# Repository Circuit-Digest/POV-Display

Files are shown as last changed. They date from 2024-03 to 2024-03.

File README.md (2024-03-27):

# [POV Display](https://circuitdigest.com/microcontroller-projects/diy-pov-display-using-ESP32-Arduino)
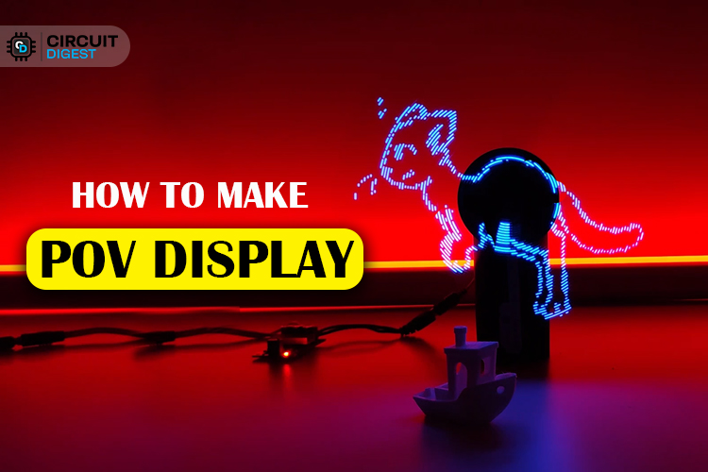
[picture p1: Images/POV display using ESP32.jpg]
image_tooltip

<br>

<br>

<be>

[DIY POV Display Tutorial using ESP32 Arduino](https://circuitdigest.com/microcontroller-projects/diy-pov-display-using-ESP32-Arduino)

[POV Display full Yoututbe Video](https://www.youtube.com/embed/gkemkTWuw_Q)

[<h1>Click here](https://circuitdigest.com/tags/ESP32) For other ESP32 tutorials.</h1>

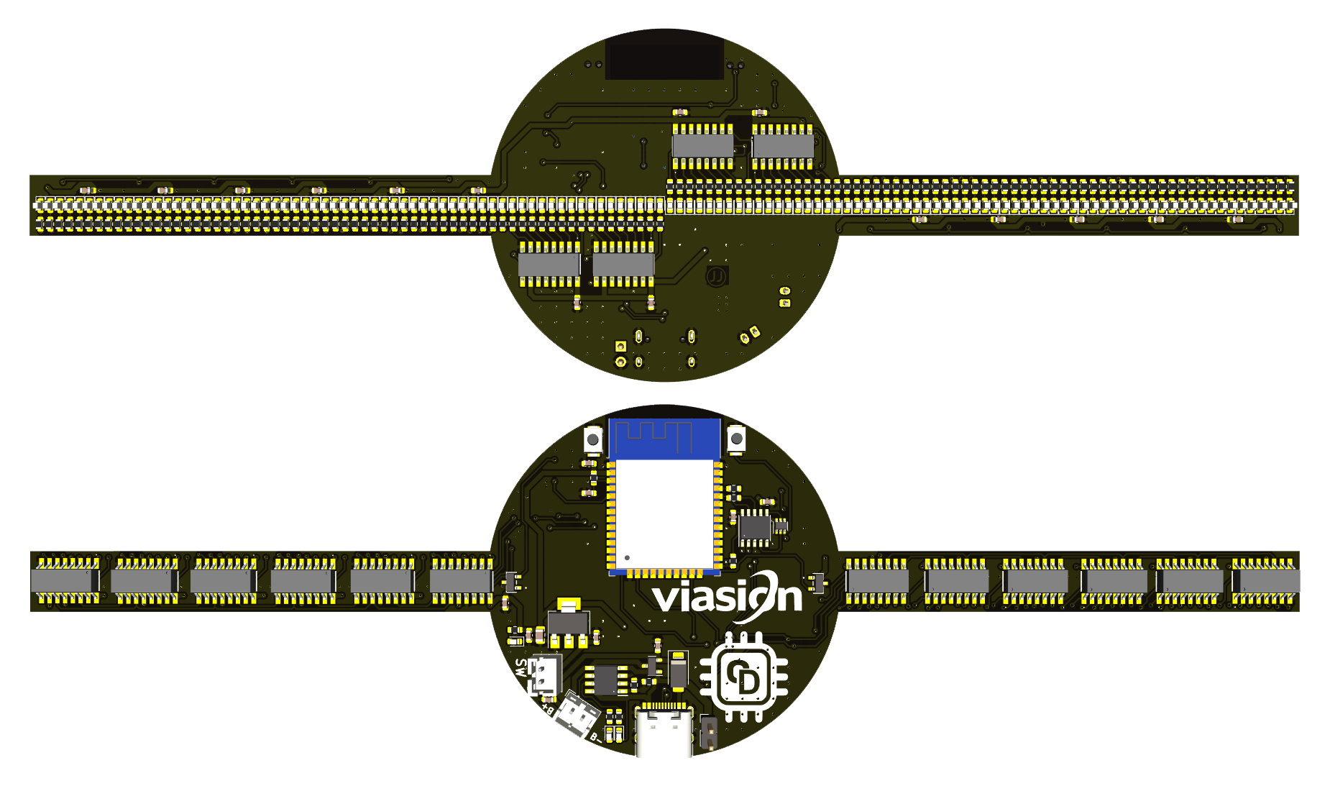
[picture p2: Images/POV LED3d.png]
image_tooltip

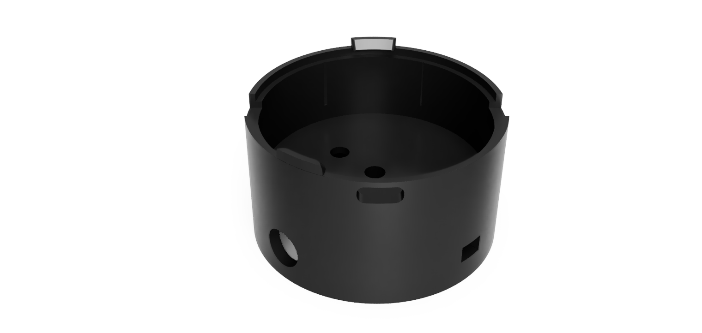
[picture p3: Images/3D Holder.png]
image_tooltip
<br>
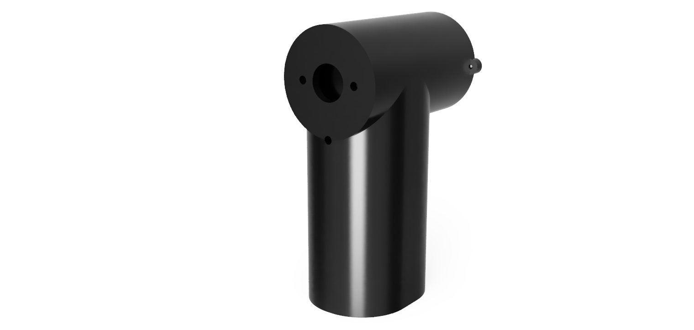
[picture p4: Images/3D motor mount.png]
image_tooltip
<br>
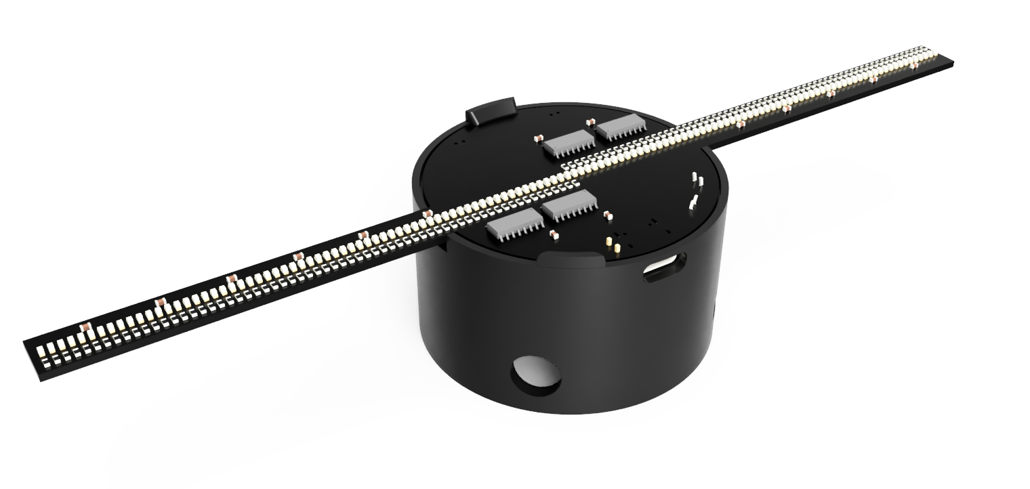
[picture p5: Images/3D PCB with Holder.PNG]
image_tooltip
<br>
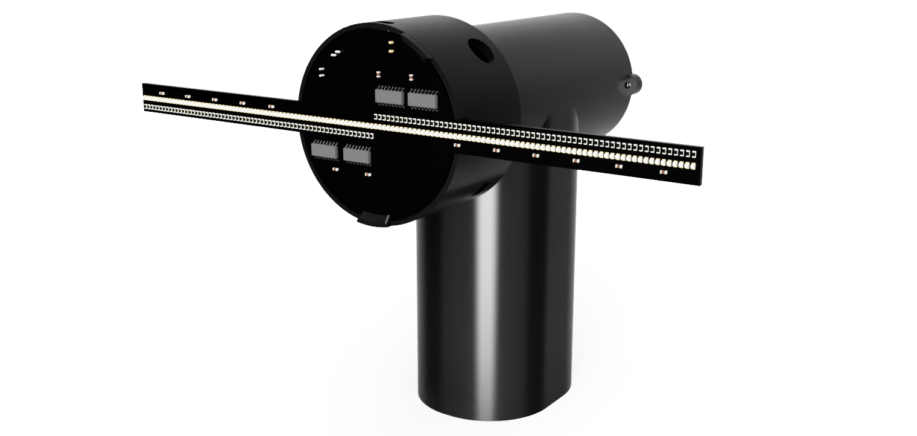
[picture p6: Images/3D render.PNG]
image_tooltip
<br>
<br>
<br>
<br>
Persistence of Vision is a fundamental principle that allows our eyes to perceive continuous motion from separate images, a concept crucial to the illusion of motion in cinema. When I was a kid, I was always fascinated with it. So, in this project, we are going to use this fascinating optical phenomenon to create a cool-looking POV Display. You must have seen a lot of such projects on the web, but most of them are limited to very low resolution and just display some texts and geometries. We plan to create a POV display that is not limited to just texts or simple shapes. Ours will be able to display images and animations with a resolution of 128 pixels. We have settled with this resolution because it's the sweet spot where we can get decent image quality and it would be easier to build.
 We settled on the ESP32 module as the brain of this display, because it is cheap, easy to get and powerful enough to run the display. The display will have two rotating arms, each outfitted with 64 LEDs, to create a total resolution of 128 pixels. The display will rotate at a constant speed, with the LEDs flashing in meticulously orchestrated patterns, controlled by the ESP32 microcontroller. This synchronization allows the display to generate images or text that appear to hover in mid-air, producing a smooth, continuous visual experience. 

<br>
[Note: As this projects are very simple we are only providing the code, schemaitic, and a few essential images if you want to get the images or code explanations do check out the Circuit Digest website.
<br>
<br>

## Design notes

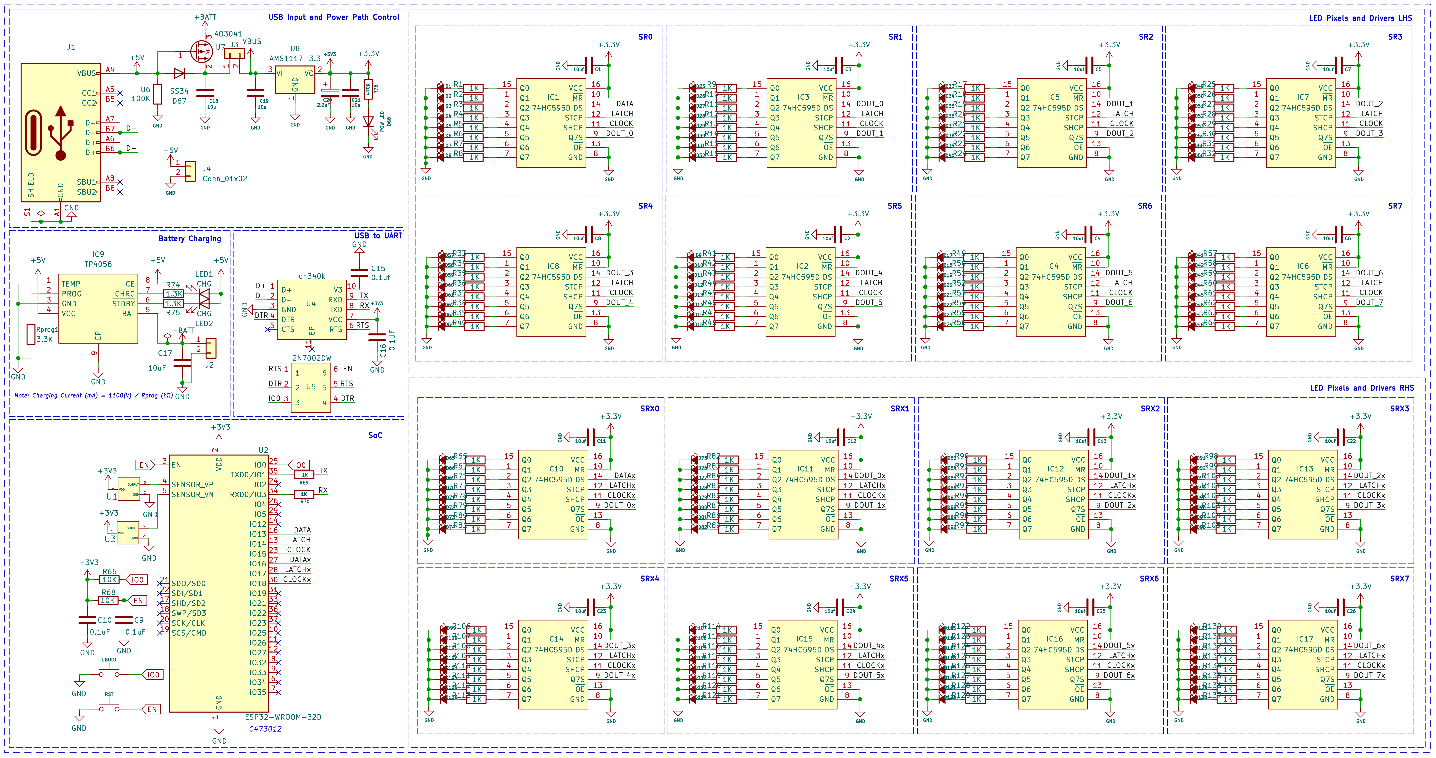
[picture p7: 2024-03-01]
PCB/Docs/Schematics POV Display.png

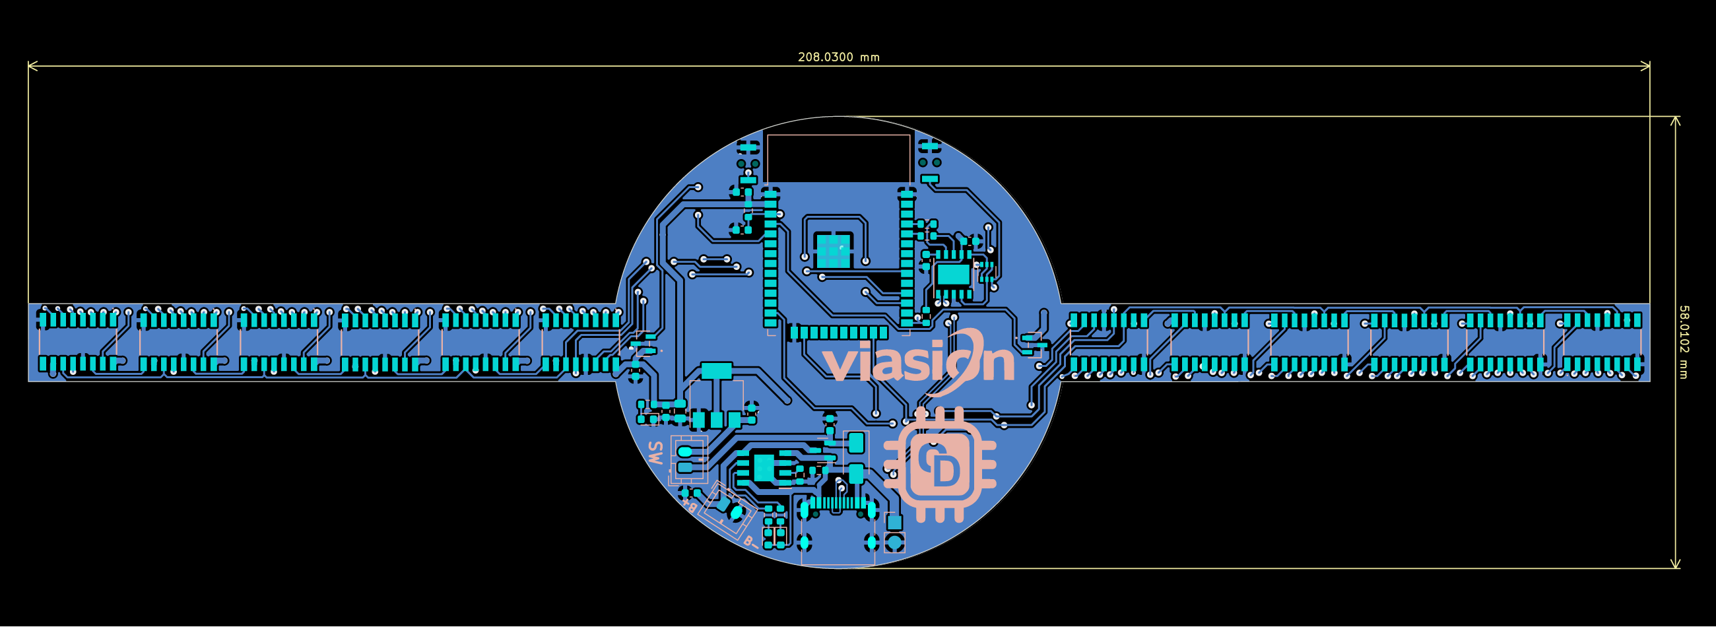
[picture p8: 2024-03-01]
PCB/Docs/POV LED-B_Cu.png

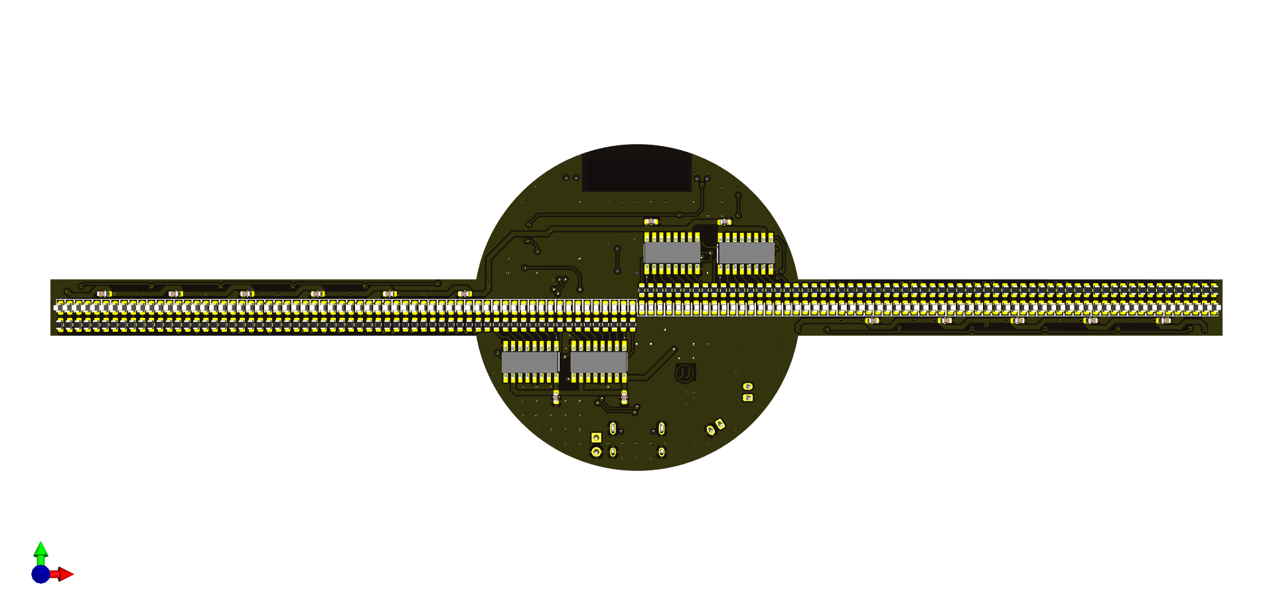
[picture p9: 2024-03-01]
Images/POV LED3d top.png

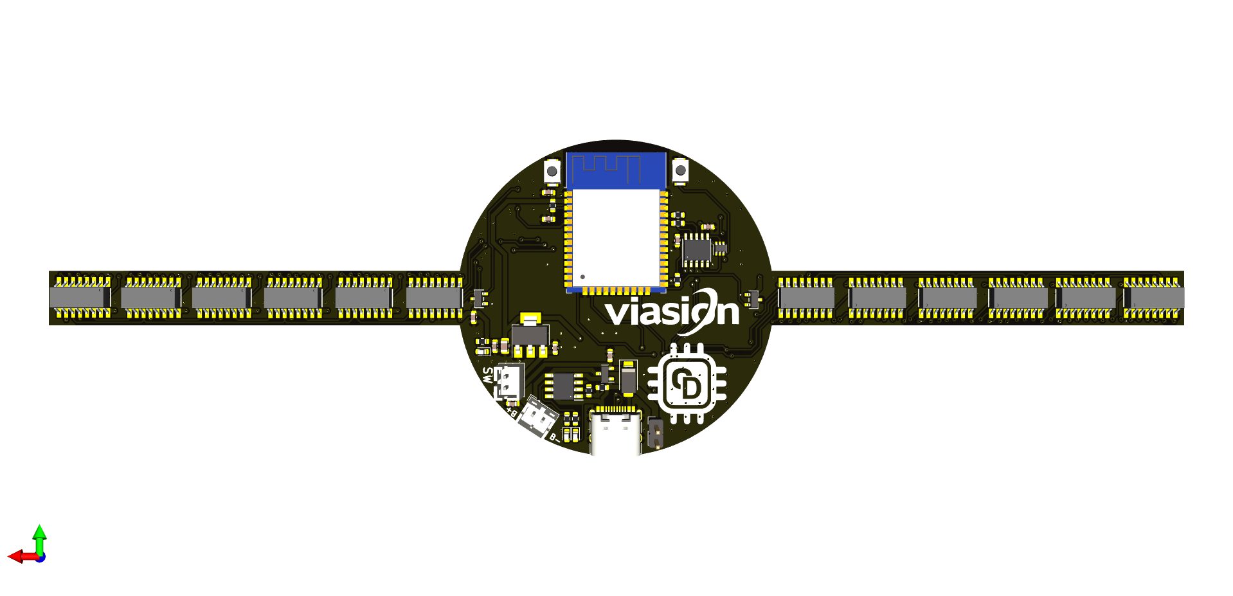
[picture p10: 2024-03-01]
Images/POV LED3d bottom.png

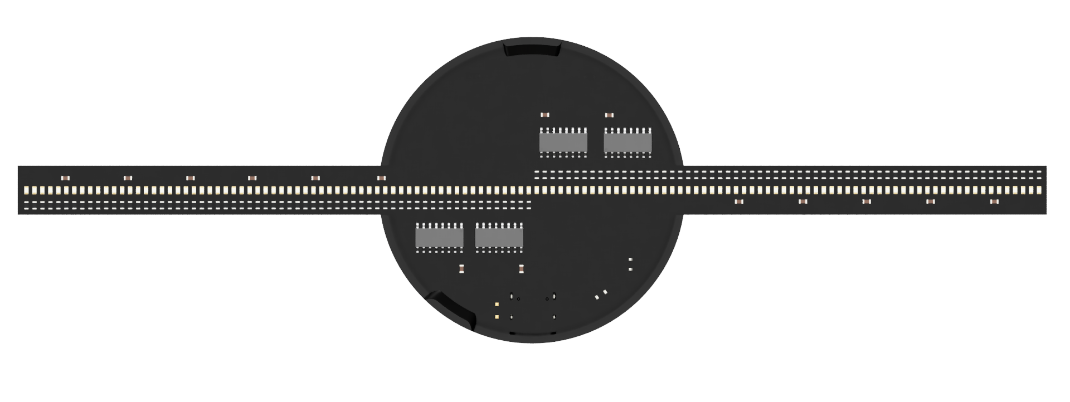
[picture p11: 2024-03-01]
Images/3D top.PNG

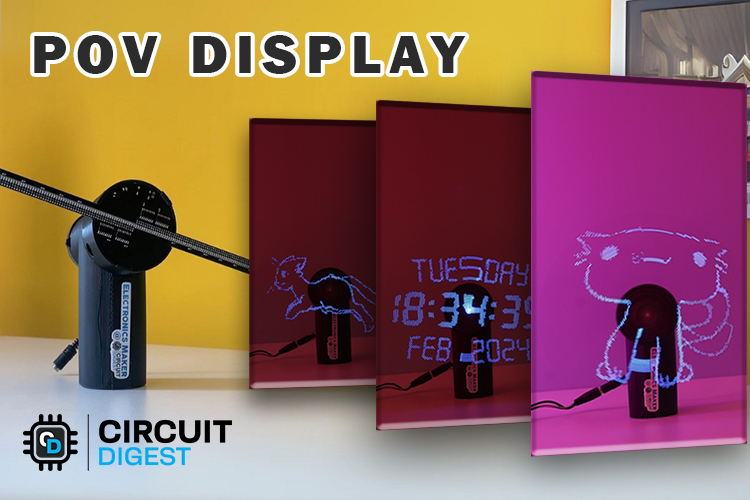
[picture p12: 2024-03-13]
Images/Title.jpg

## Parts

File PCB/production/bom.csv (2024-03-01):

Designator | Footprint | Quantity | Value | LCSC Part #
BOOT1 | Tactile 3x4x2mm TS-A010 | 1 | UBOOT
C1, C11, C12, C13, C17, C2, C22, C23, C24, C25, C26, C3, C4, C5, C6, C7, C8 | 0603 | 17 | 10uf
C10, C15, C16, C9 | 0603 | 4 | 0.1uF
C18, C19, C21 | 0603 | 3 | 10u
C20 | 0805 | 1 | 2.2uF
D1, D10, D100, D101, D102, D103, D104, D105, D106, D107, D108, D109, D11, D110, D111, D112, D113, D114, D115, D116, D117, D118, D119, D12, D120, D121, D122, D123, D124, D125, D126, D127, D128, D129, D13, D130, D14, D15, D16, D17, D18, D19, D2, D20, D21, D22, D23, D24, D25, D26, D27, D28, D29, D3, D30, D31, D32, D33, D34, D35, D36, D37, D38, D39, D4, D40, D41, D42, D43, D44, D45, D46, D47, D48, D49, D5, D50, D51, D52, D53, D54, D55, D56, D57, D58, D59, D6, D60, D61, D62, D63, D64, D65, D66, D69, D7, D70, D71, D72, D73, D74, D75, D76, D77, D78, D79, D8, D80, D81, D82, D83, D84, D85, D86, D87, D88, D89, D9, D90, D91, D92, D93, D94, D95, D96, D97, D98, D99 | 0603 | 128 | LED_Small_Filled
D67 | D_SMA | 1 | SS34
D68 | 0603 | 1 | POW_LED
IC1, IC10, IC11, IC12, IC13, IC14, IC15, IC16, IC17, IC2, IC3, IC4, IC5, IC6, IC7, IC8 | 74HC595DQ100118 | 16 | 74HC595D
IC9 | SOIC127P600X175-9N | 1 | TP4056
J1 | USB_C_Receptacle_HRO_TYPE-C-31-M-12 | 1 | USB_C_Receptacle_USB2.0
J2, J3 | JST_PH_B2B-PH-K_1x02_P2.00mm_Vertical | 2 | B2B-PH-SM4-TB(LF)(SN)
J4 | PinHeader_1x02_P2.54mm_Vertical | 1 | Conn_01x02
LED1, LED2 | 0603 | 2 | CHG
R1, R10, R100, R101, R102, R103, R104, R105, R106, R107, R108, R109, R11, R110, R111, R112, R113, R114, R115, R116, R117, R118, R119, R12, R120, R121, R122, R123, R124, R125, R126, R127, R128, R129, R13, R130, R131, R132, R133, R134, R135, R136, R137, R14, R15, R16, R17, R18, R19, R2, R20, R21, R22, R23, R24, R25, R26, R27, R28, R29, R3, R30, R31, R32, R33, R34, R35, R36, R37, R38, R39, R4, R40, R41, R42, R43, R44, R45, R46, R47, R48, R49, R5, R50, R51, R52, R53, R54, R55, R56, R57, R58, R59, R6, R60, R61, R62, R63, R64, R65, R67, R69, R7, R70, R71, R77, R78, R79, R8, R80, R81, R82, R83, R84, R85, R86, R87, R88, R89, R9, R90, R91, R92, R93, R94, R95, R96, R97, R98, R99 | 0603 | 130 | 1K
R66, R68 | 0603 | 2 | 10K
R74, R75 | 0603 | 2 | 1.3K
R76 | 0603 | 1 | 470R
RST1 | Tactile 3x4x2mm TS-A010 | 1 | RST
Rprog1 | 0603 | 1 | 3.3K
U1, U3 | SOT23_AH3572-SA-7_DIO | 2 | AH3572-SA-7
U2 | ESP32-WROOM-32 | 1 | ESP32-WROOM-32D
U4 | ESSOP-10_3.9x4.9mm_P1.00mm | 1 | ch340k
U5 | SOT-363_SC-70-6 | 1 | DDC114TU-7-F
U6 | 0603 | 1 | 100K
U7 | SOT-23 | 1 | AO3041
U8 | SOT-223-3_TabPin2 | 1 | AMS1117-3.3

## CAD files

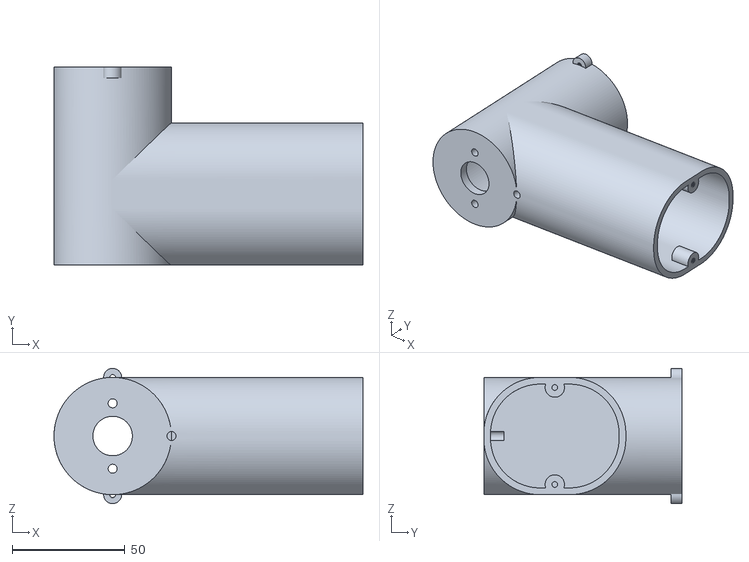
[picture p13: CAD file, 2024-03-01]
3D files/Motor Mount.stl
137.0 x 88.0 x 60.0

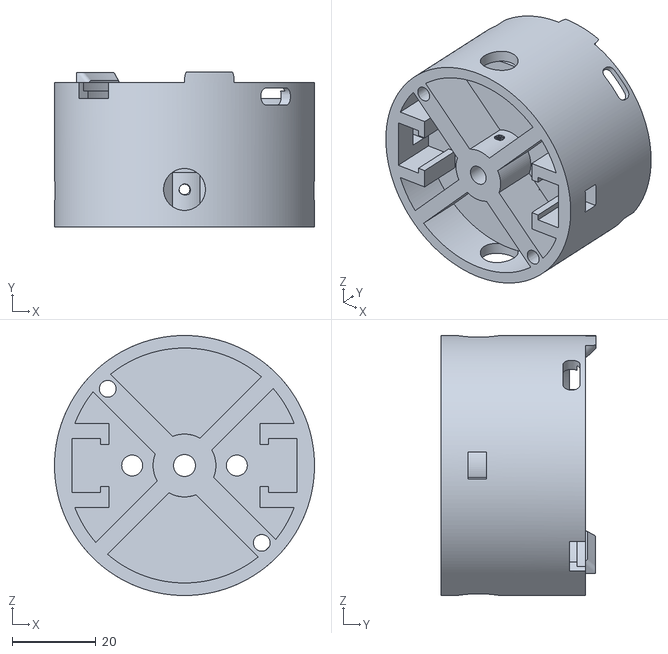
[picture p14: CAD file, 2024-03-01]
3D files/PCB Mount.stl
62.1 x 37.1 x 62.1

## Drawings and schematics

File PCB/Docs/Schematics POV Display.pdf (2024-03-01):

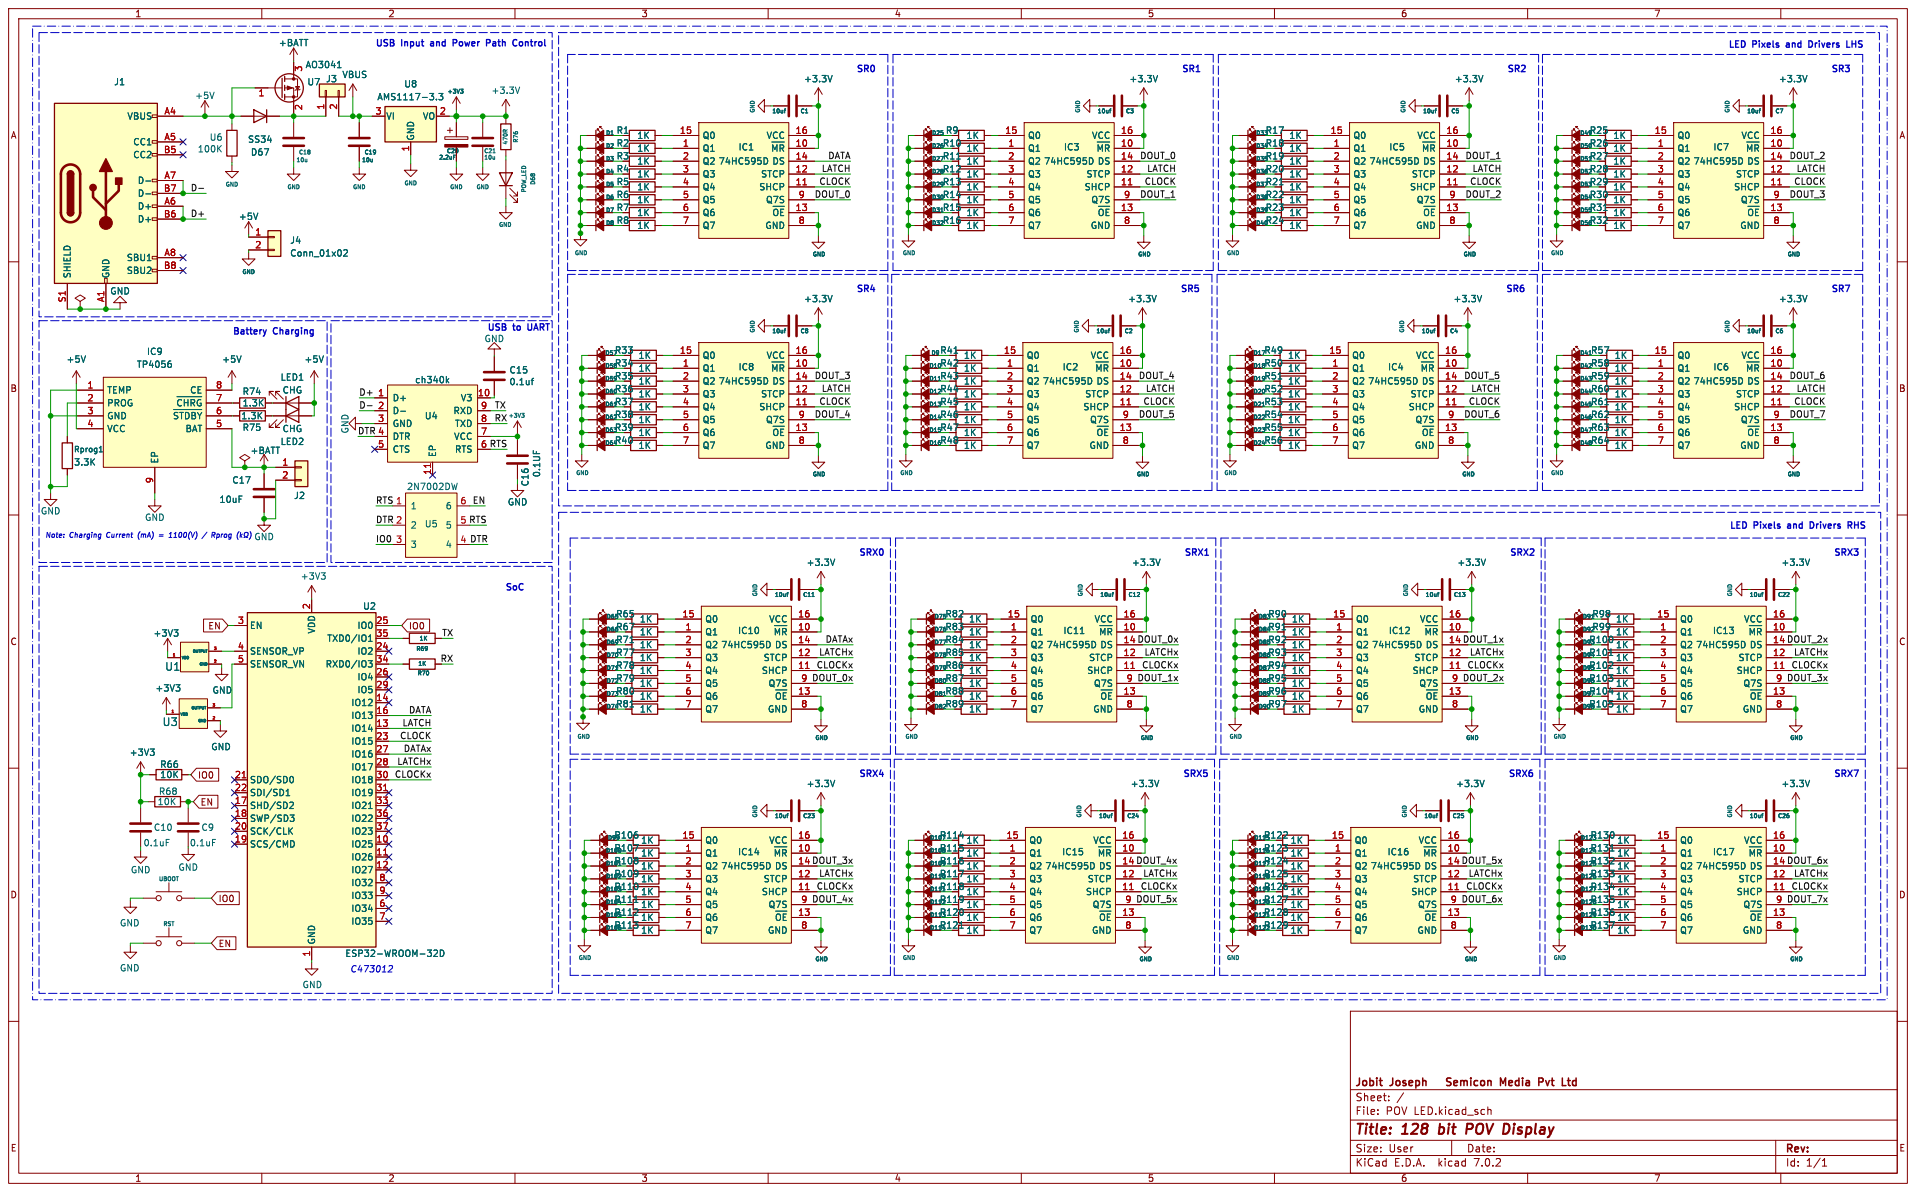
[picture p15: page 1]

USB Input and Power Path Control

LED Pixels and Drivers LHS

2 SCK/CLK 20 SDO/SD0 21 SDI/SD1 22

Id: 1/1 Title: 128 bit POV Display

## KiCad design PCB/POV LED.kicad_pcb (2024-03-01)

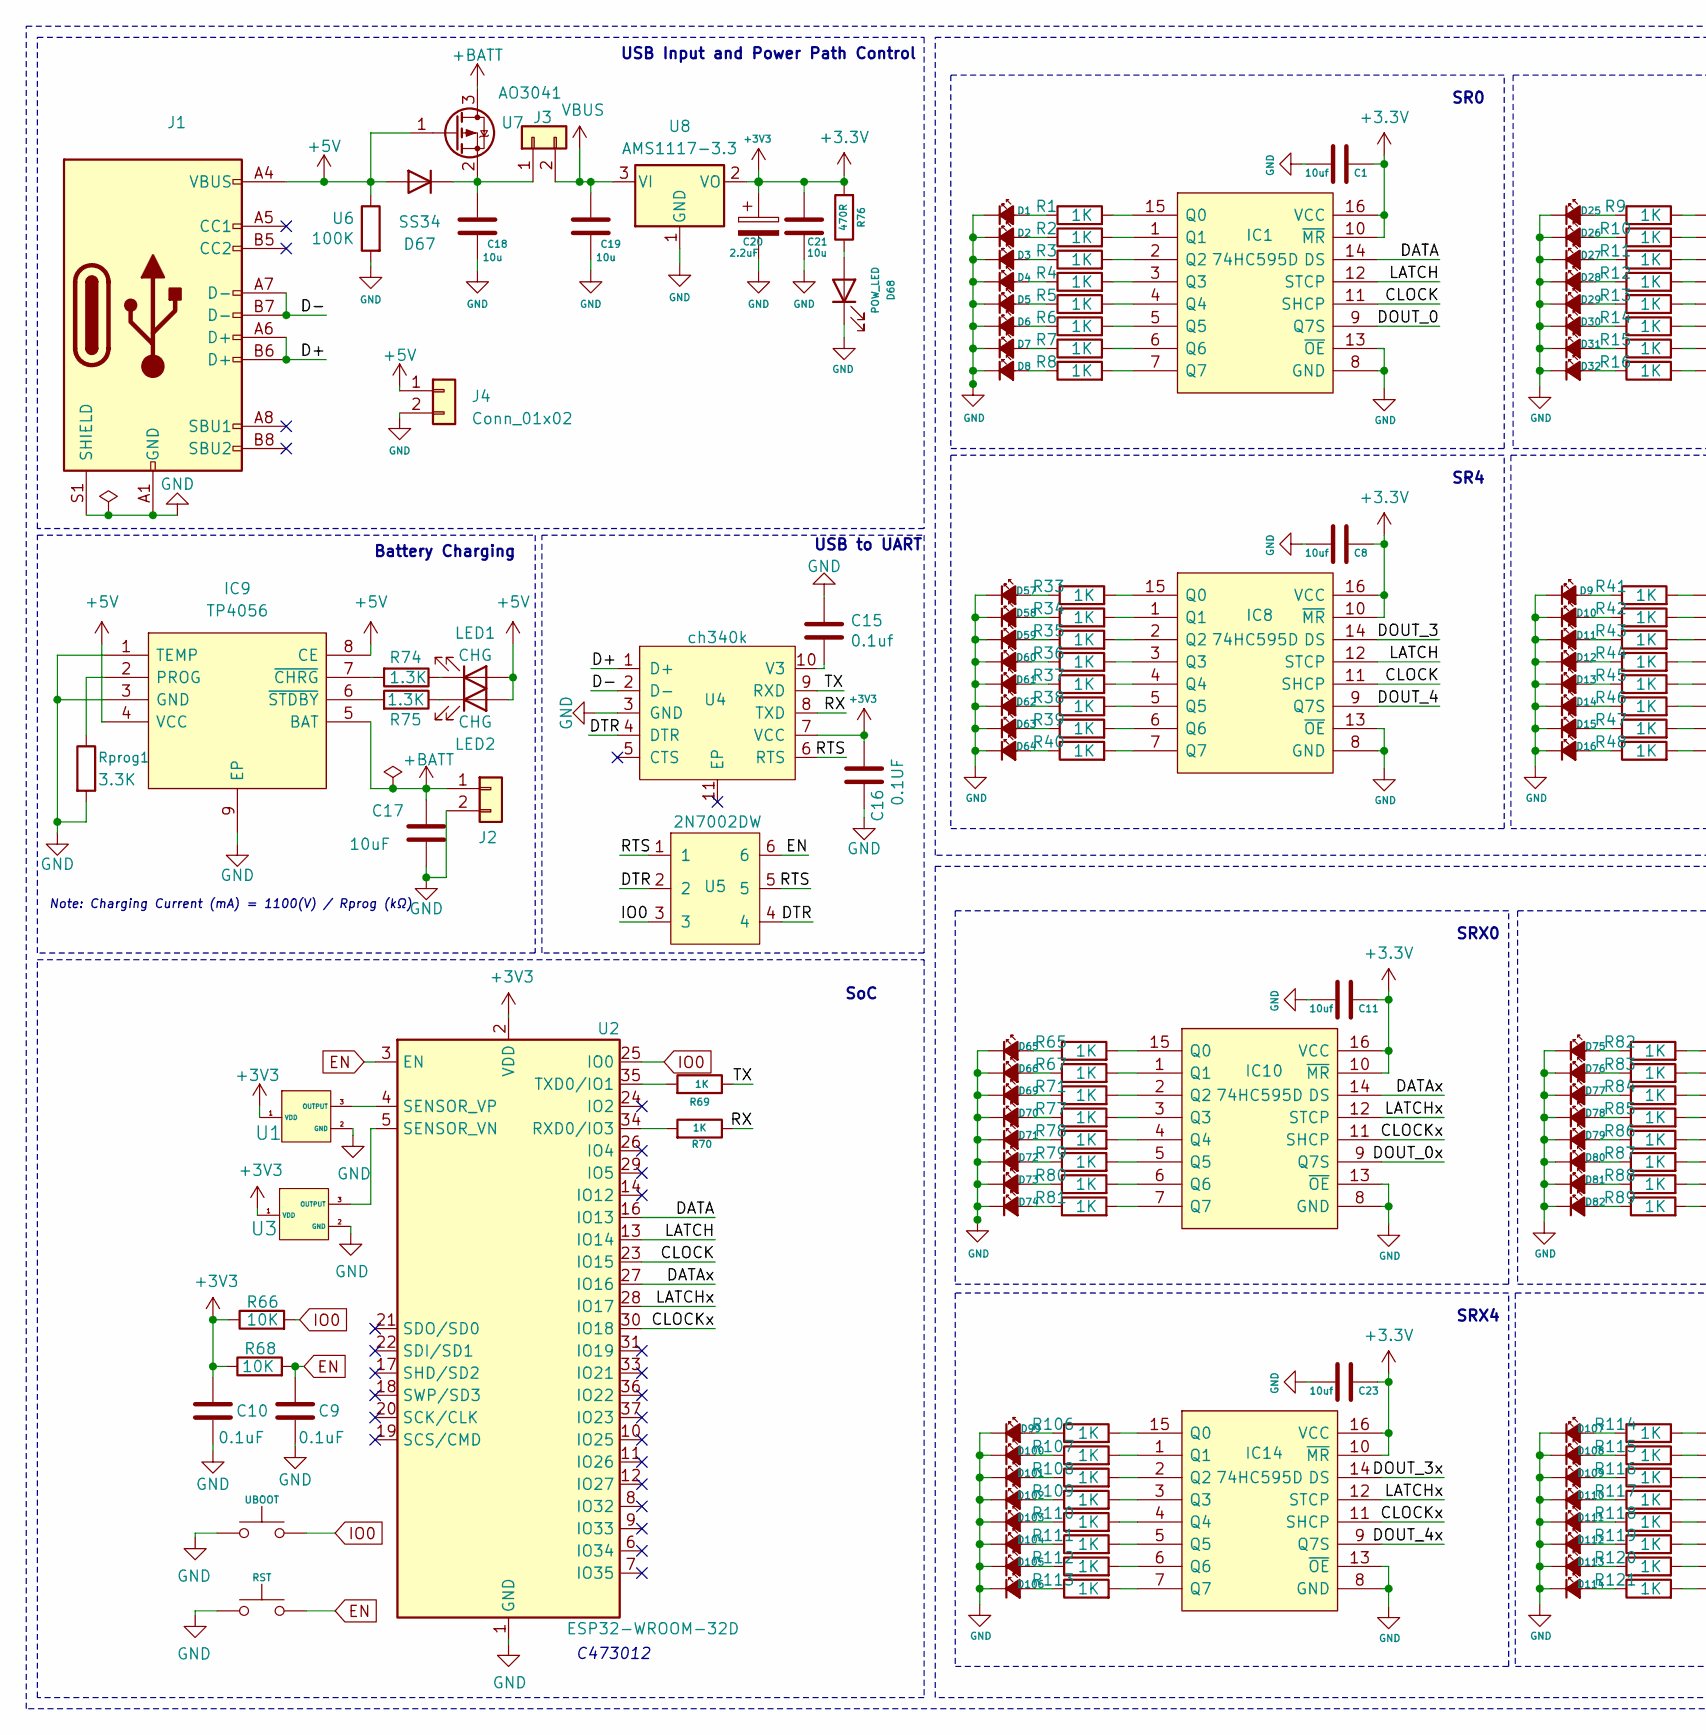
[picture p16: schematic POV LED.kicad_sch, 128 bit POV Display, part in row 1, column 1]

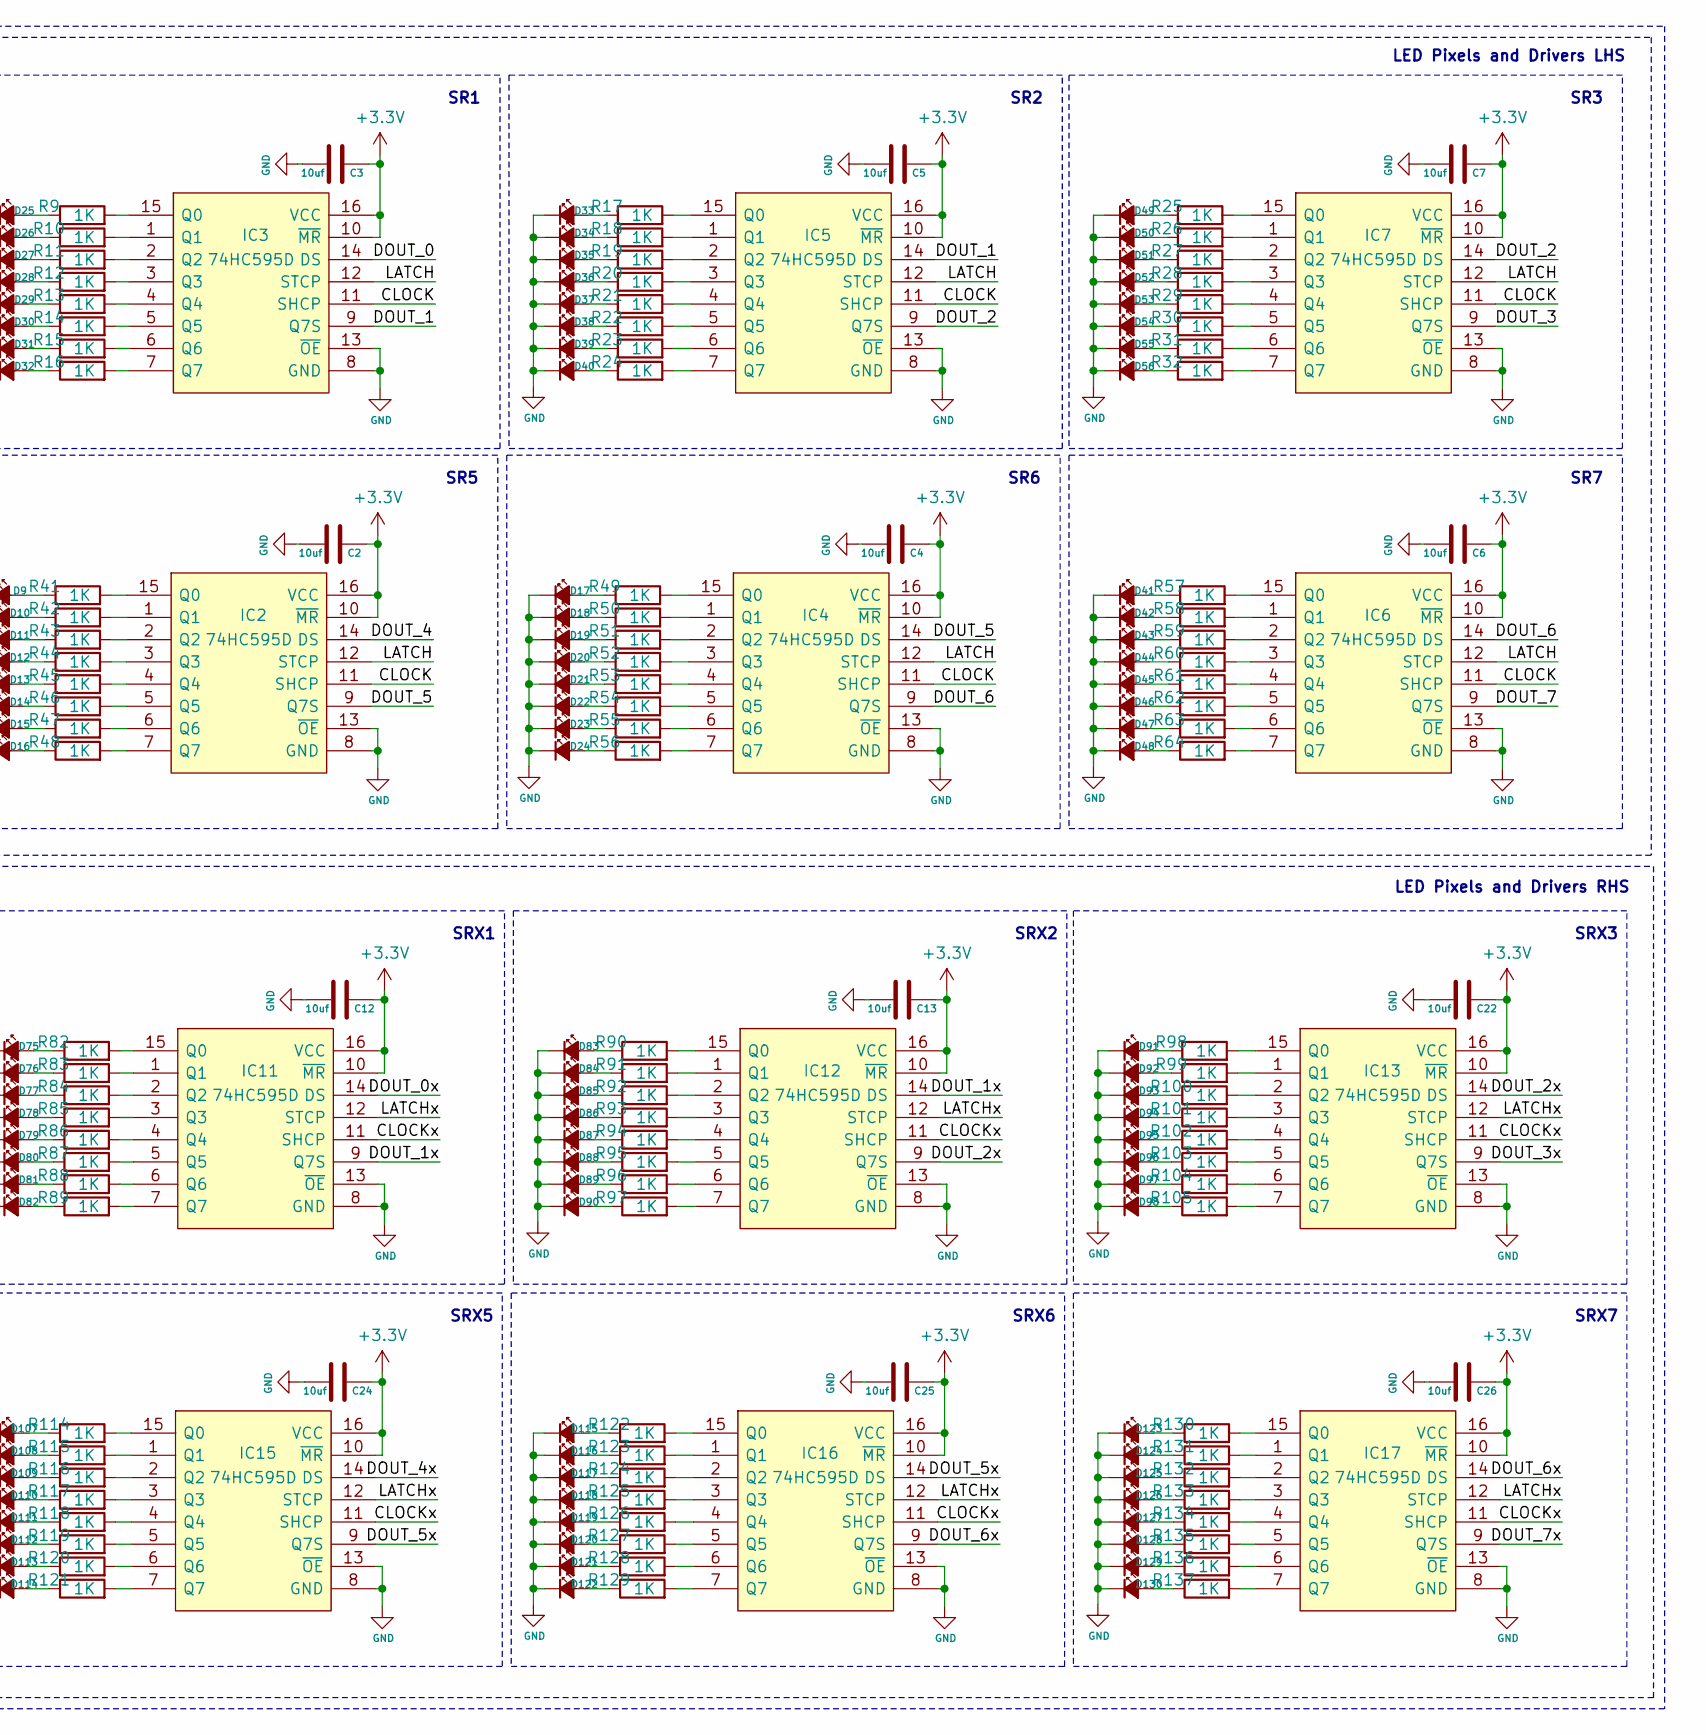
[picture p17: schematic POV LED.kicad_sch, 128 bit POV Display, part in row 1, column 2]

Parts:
BOOT1: UBOOT; Tactile 3x4x2mm TS-A010
C1, C2, C3, C4, C5, C6, C7, C8, C11, C12, C13, C22, C23, C24, C25, C26: 10uf; C_0603_1608Metric
C9, C10: 0.1uF; C_0603_1608Metric
C15: 0.1uf; C_0603_1608Metric
C16: 0.1UF; C_0603_1608Metric
C17: 10uF; C_0603_1608Metric
C18, C19, C21: 10u; C_0603_1608Metric
C20: 2.2uF; C_0805_2012Metric
D1, D2, D3, D4, D5, D6, D7, D8, D9, D10, D11, D12, D13, D14, D15, D16, D17, D18, D19, D20, D21, D22, D23, D24, D25, D26, D27, D28, D29, D30, D31, D32, D33, D34, D35, D36, D37, D38, D39, D40, D41, D42, D43, D44, D45, D46, D47, D48, D49, D50, D51, D52, D53, D54, D55, D56, D57, D58, D59, D60, D61, D62, D63, D64, D65, D66, D69, D70, D71, D72, D73, D74, D75, D76, D77, D78, D79, D80, D81, D82, D83, D84, D85, D86, D87, D88, D89, D90, D91, D92, D93, D94, D95, D96, D97, D98, D99, D100, D101, D102, D103, D104, D105, D106, D107, D108, D109, D110, D111, D112, D113, D114, D115, D116, D117, D118, D119, D120, D121, D122, D123, D124, D125, D126, D127, D128, D129, D130: LED_Small_Filled; LED_0603_1608Metric
D67: SS34; D_SMA
D68: POW_LED; LED_0603_1608Metric
IC1, IC2, IC3, IC4, IC5, IC6, IC7, IC8, IC10, IC11, IC12, IC13, IC14, IC15, IC16, IC17: 74HC595D; 74HC595DQ100118; Mouser Part Number 771-74HC595D-Q100
IC9: TP4056; SOIC127P600X175-9N; Manufacturer_Part_Number TP4056-42-ESOP8
J1: USB_C_Receptacle_USB2.0; USB_C_Receptacle_HRO_TYPE-C-31-M-12
J2, J3: B2B-PH-SM4-TB(LF)(SN); JST_PH_B2B-PH-K_1x02_P2.00mm_Vertical
J4: Conn_01x02; PinHeader_1x02_P2.54mm_Vertical
LED1, LED2: CHG; LED_0603_1608Metric
R1, R2, R3, R4, R5, R6, R7, R8, R9, R10, R11, R12, R13, R14, R15, R16, R17, R18, R19, R20, R21, R22, R23, R24, R25, R26, R27, R28, R29, R30, R31, R32, R33, R34, R35, R36, R37, R38, R39, R40, R41, R42, R43, R44, R45, R46, R47, R48, R49, R50, R51, R52, R53, R54, R55, R56, R57, R58, R59, R60, R61, R62, R63, R64, R65, R67, R69, R70, R71, R77, R78, R79, R80, R81, R82, R83, R84, R85, R86, R87, R88, R89, R90, R91, R92, R93, R94, R95, R96, R97, R98, R99, R100, R101, R102, R103, R104, R105, R106, R107, R108, R109, R110, R111, R112, R113, R114, R115, R116, R117, R118, R119, R120, R121, R122, R123, R124, R125, R126, R127, R128, R129, R130, R131, R132, R133, R134, R135, R136, R137: 1K; R_0603_1608Metric
R66, R68: 10K; R_0603_1608Metric
R74, R75: 1.3K; R_0603_1608Metric
R76: 470R; R_0603_1608Metric
RST1: RST; Tactile 3x4x2mm TS-A010
Rprog1: 3.3K; R_0603_1608Metric
U1, U3: AH3572-SA-7; SOT23_AH3572-SA-7_DIO
U2: ESP32-WROOM-32D; ESP32-WROOM-32
U4: ch340k; ESSOP-10_3.9x4.9mm_P1.00mm
U5: 2N7002DW; SOT-363_SC-70-6
U6: 100K; R_0603_1608Metric
U7: AO3041; SOT-23
U8: AMS1117-3.3; SOT-223-3_TabPin2

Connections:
+3.3V: C1.1, C2.1, C3.1, C4.1, C5.1, C6.1, C7.1, C8.1, C10.1, C11.1, C12.1, C13.1, C16.2, C20.1, C21.1, C22.1, C23.1, C24.1, C25.1, C26.1, IC1.10 (~MR), IC1.16 (VCC), IC2.10 (~MR), IC2.16 (VCC), IC3.10 (~MR), IC3.16 (VCC), IC4.10 (~MR), IC4.16 (VCC), IC5.10 (~MR), IC5.16 (VCC), IC6.10 (~MR), IC6.16 (VCC), IC7.10 (~MR), IC7.16 (VCC), IC8.10 (~MR), IC8.16 (VCC), IC10.10 (~MR), IC10.16 (VCC), IC11.10 (~MR), IC11.16 (VCC), IC12.10 (~MR), IC12.16 (VCC), IC13.10 (~MR), IC13.16 (VCC), IC14.10 (~MR), IC14.16 (VCC), IC15.10 (~MR), IC15.16 (VCC), IC16.10 (~MR), IC16.16 (VCC), IC17.10 (~MR), IC17.16 (VCC), R66.1, R68.1, R76.2, U1.1 (VDD), U2.2 (VDD), U3.1 (VDD), U4.7 (VCC), U8.2 (VO)
+5V: D67.2 (A), IC9.4 (VCC), IC9.8 (CE), J1.A4 (VBUS), J1.A9 (VBUS), J1.B4 (VBUS), J1.B9 (VBUS), J4.1, LED1.2 (A), LED2.2 (A), U6.1, U7.1 (G)
+BATT: C17.1, IC9.5 (BAT), J2.1, U7.3 (D)
/CLOCK: IC1.11 (SHCP), IC2.11 (SHCP), IC3.11 (SHCP), IC4.11 (SHCP), IC5.11 (SHCP), IC6.11 (SHCP), IC7.11 (SHCP), IC8.11 (SHCP), U2.23 (IO15)
/CLOCKx: IC10.11 (SHCP), IC11.11 (SHCP), IC12.11 (SHCP), IC13.11 (SHCP), IC14.11 (SHCP), IC15.11 (SHCP), IC16.11 (SHCP), IC17.11 (SHCP), U2.30 (IO18)
/D+: J1.A6 (D+), J1.B6 (D+), U4.1 (D+)
/D-: J1.A7 (D-), J1.B7 (D-), U4.2 (D-)
/DATA: IC1.14 (DS), U2.16 (IO13)
/DATAx: IC10.14 (DS), U2.27 (IO16)
/DOUT_0: IC1.9 (Q7S), IC3.14 (DS)
/DOUT_0x: IC10.9 (Q7S), IC11.14 (DS)
/DOUT_1: IC3.9 (Q7S), IC5.14 (DS)
/DOUT_1x: IC11.9 (Q7S), IC12.14 (DS)
/DOUT_2: IC5.9 (Q7S), IC7.14 (DS)
/DOUT_2x: IC12.9 (Q7S), IC13.14 (DS)
/DOUT_3: IC7.9 (Q7S), IC8.14 (DS)
/DOUT_3x: IC13.9 (Q7S), IC14.14 (DS)
/DOUT_4: IC2.14 (DS), IC8.9 (Q7S)
/DOUT_4x: IC14.9 (Q7S), IC15.14 (DS)
/DOUT_5: IC2.9 (Q7S), IC4.14 (DS)
/DOUT_5x: IC15.9 (Q7S), IC16.14 (DS)
/DOUT_6: IC4.9 (Q7S), IC6.14 (DS)
/DOUT_6x: IC16.9 (Q7S), IC17.14 (DS)
/DOUT_7: IC6.9 (Q7S)
/DOUT_7x: IC17.9 (Q7S)
/DTR: U4.4 (DTR), U5.2, U5.4
/LATCH: IC1.12 (STCP), IC2.12 (STCP), IC3.12 (STCP), IC4.12 (STCP), IC5.12 (STCP), IC6.12 (STCP), IC7.12 (STCP), IC8.12 (STCP), U2.13 (IO14)
/LATCHx: IC10.12 (STCP), IC11.12 (STCP), IC12.12 (STCP), IC13.12 (STCP), IC14.12 (STCP), IC15.12 (STCP), IC16.12 (STCP), IC17.12 (STCP), U2.28 (IO17)
/RTS: U4.6 (RTS), U5.1, U5.5
/RX: R70.1, U4.8 (TXD)
/TX: R69.1, U4.9 (RXD)
EN: C9.1, R68.2, RST1.1, U2.3 (EN), U5.6
GND: BOOT1.2, C1.2, C2.2, C3.2, C4.2, C5.2, C6.2, C7.2, C8.2, C9.2, C10.2, C11.2, C12.2, C13.2, C15.1, C16.1, C17.2, C18.2, C19.2, C20.2, C21.2, C22.2, C23.2, C24.2, C25.2, C26.2, D1.1 (K), D2.1 (K), D3.1 (K), D4.1 (K), D5.1 (K), D6.1 (K), D7.1 (K), D8.1 (K), D9.1 (K), D10.1 (K), D11.1 (K), D12.1 (K), D13.1 (K), D14.1 (K), D15.1 (K), D16.1 (K), D17.1 (K), D18.1 (K), D19.1 (K), D20.1 (K), D21.1 (K), D22.1 (K), D23.1 (K), D24.1 (K), D25.1 (K), D26.1 (K), D27.1 (K), D28.1 (K), D29.1 (K), D30.1 (K), D31.1 (K), D32.1 (K), D33.1 (K), D34.1 (K), D35.1 (K), D36.1 (K), D37.1 (K), D38.1 (K), D39.1 (K), D40.1 (K), D41.1 (K), D42.1 (K), D43.1 (K), D44.1 (K), D45.1 (K), D46.1 (K), D47.1 (K), D48.1 (K), D49.1 (K), D50.1 (K), D51.1 (K), D52.1 (K), D53.1 (K), D54.1 (K), D55.1 (K), D56.1 (K), D57.1 (K), D58.1 (K), D59.1 (K), D60.1 (K), D61.1 (K), D62.1 (K), D63.1 (K), D64.1 (K), D65.1 (K), D66.1 (K), D68.1 (K), D69.1 (K), D70.1 (K), D71.1 (K), D72.1 (K), D73.1 (K), D74.1 (K), D75.1 (K), D76.1 (K), D77.1 (K), D78.1 (K), D79.1 (K), D80.1 (K), D81.1 (K), D82.1 (K), D83.1 (K), D84.1 (K), D85.1 (K), D86.1 (K), D87.1 (K), D88.1 (K), D89.1 (K), D90.1 (K), D91.1 (K), D92.1 (K), D93.1 (K), D94.1 (K), D95.1 (K), D96.1 (K), D97.1 (K), D98.1 (K), D99.1 (K), D100.1 (K), D101.1 (K), D102.1 (K), D103.1 (K), D104.1 (K), D105.1 (K), D106.1 (K), D107.1 (K), D108.1 (K), D109.1 (K), D110.1 (K), D111.1 (K), D112.1 (K), D113.1 (K), D114.1 (K), D115.1 (K), D116.1 (K), D117.1 (K), D118.1 (K), D119.1 (K), D120.1 (K), D121.1 (K), D122.1 (K), D123.1 (K), D124.1 (K), D125.1 (K), D126.1 (K), D127.1 (K), D128.1 (K), D129.1 (K), D130.1 (K), IC1.8 (GND), IC1.13 (~OE), IC2.8 (GND), IC2.13 (~OE), IC3.8 (GND), IC3.13 (~OE), IC4.8 (GND), IC4.13 (~OE), IC5.8 (GND), IC5.13 (~OE), IC6.8 (GND), IC6.13 (~OE), IC7.8 (GND), IC7.13 (~OE), IC8.8 (GND), IC8.13 (~OE), IC9.1 (TEMP), IC9.3 (GND), IC9.9 (EP), IC10.8 (GND), IC10.13 (~OE), IC11.8 (GND), IC11.13 (~OE), IC12.8 (GND), IC12.13 (~OE), IC13.8 (GND), IC13.13 (~OE), IC14.8 (GND), IC14.13 (~OE), IC15.8 (GND), IC15.13 (~OE), IC16.8 (GND), IC16.13 (~OE), IC17.8 (GND), IC17.13 (~OE), J1.A1 (GND), J1.A12 (GND), J1.B1 (GND), J1.B12 (GND), J1.S1 (SHIELD), J2.2, J4.2, RST1.2, Rprog1.2, U1.2 (GND), U2.1 (GND), U2.15 (GND), U2.38 (GND), U2.39 (GND), U3.2 (GND), U4.3 (GND), U6.2, U8.1 (GND)
IO0: BOOT1.1, R66.2, U2.25 (IO0), U5.3
unnamed: D1.2 (A), R1.1
unnamed: D2.2 (A), R2.1
unnamed: D3.2 (A), R3.1
unnamed: D4.2 (A), R4.1
unnamed: D5.2 (A), R5.1
unnamed: D6.2 (A), R6.1
unnamed: D7.2 (A), R7.1
unnamed: D8.2 (A), R8.1
unnamed: D9.2 (A), R41.1
unnamed: D10.2 (A), R42.1
unnamed: D11.2 (A), R43.1
unnamed: D12.2 (A), R44.1
unnamed: D13.2 (A), R45.1
unnamed: D14.2 (A), R46.1
unnamed: D15.2 (A), R47.1
unnamed: D16.2 (A), R48.1
unnamed: D17.2 (A), R49.1
unnamed: D18.2 (A), R50.1
unnamed: D19.2 (A), R51.1
unnamed: D20.2 (A), R52.1
unnamed: D21.2 (A), R53.1
unnamed: D22.2 (A), R54.1
unnamed: D23.2 (A), R55.1
unnamed: D24.2 (A), R56.1
unnamed: D25.2 (A), R9.1
unnamed: D26.2 (A), R10.1
unnamed: D27.2 (A), R11.1
unnamed: D28.2 (A), R12.1
unnamed: D29.2 (A), R13.1
unnamed: D30.2 (A), R14.1
unnamed: D31.2 (A), R15.1
unnamed: D32.2 (A), R16.1
unnamed: D33.2 (A), R17.1
unnamed: D34.2 (A), R18.1
unnamed: D35.2 (A), R19.1
unnamed: D36.2 (A), R20.1
unnamed: D37.2 (A), R21.1
unnamed: D38.2 (A), R22.1
unnamed: D39.2 (A), R23.1
unnamed: D40.2 (A), R24.1
unnamed: D41.2 (A), R57.1
unnamed: D42.2 (A), R58.1
unnamed: D43.2 (A), R59.1
unnamed: D44.2 (A), R60.1
unnamed: D45.2 (A), R61.1
unnamed: D46.2 (A), R62.1
unnamed: D47.2 (A), R63.1
unnamed: D48.2 (A), R64.1
unnamed: D49.2 (A), R25.1
unnamed: D50.2 (A), R26.1
unnamed: D51.2 (A), R27.1
unnamed: D52.2 (A), R28.1
unnamed: D53.2 (A), R29.1
unnamed: D54.2 (A), R30.1
unnamed: D55.2 (A), R31.1
unnamed: D56.2 (A), R32.1
unnamed: D57.2 (A), R33.1
unnamed: D58.2 (A), R34.1
unnamed: D59.2 (A), R35.1
unnamed: D60.2 (A), R36.1
unnamed: D61.2 (A), R37.1
unnamed: D62.2 (A), R38.1
unnamed: D63.2 (A), R39.1
unnamed: D64.2 (A), R40.1
unnamed: D65.2 (A), R65.1
unnamed: D66.2 (A), R67.1
unnamed: C18.1, D67.1 (K), J3.1, U7.2 (S)
unnamed: D68.2 (A), R76.1
unnamed: D69.2 (A), R71.1
unnamed: D70.2 (A), R77.1
unnamed: D71.2 (A), R78.1
unnamed: D72.2 (A), R79.1
unnamed: D73.2 (A), R80.1
unnamed: D74.2 (A), R81.1
unnamed: D75.2 (A), R82.1
unnamed: D76.2 (A), R83.1
unnamed: D77.2 (A), R84.1
unnamed: D78.2 (A), R85.1
unnamed: D79.2 (A), R86.1
unnamed: D80.2 (A), R87.1
unnamed: D81.2 (A), R88.1
unnamed: D82.2 (A), R89.1
unnamed: D83.2 (A), R90.1
unnamed: D84.2 (A), R91.1
unnamed: D85.2 (A), R92.1
unnamed: D86.2 (A), R93.1
unnamed: D87.2 (A), R94.1
unnamed: D88.2 (A), R95.1
unnamed: D89.2 (A), R96.1
unnamed: D90.2 (A), R97.1
unnamed: D91.2 (A), R98.1
unnamed: D92.2 (A), R99.1
unnamed: D93.2 (A), R100.1
unnamed: D94.2 (A), R101.1
unnamed: D95.2 (A), R102.1
unnamed: D96.2 (A), R103.1
unnamed: D97.2 (A), R104.1
unnamed: D98.2 (A), R105.1
unnamed: D99.2 (A), R106.1
unnamed: D100.2 (A), R107.1
unnamed: D101.2 (A), R108.1
unnamed: D102.2 (A), R109.1
unnamed: D103.2 (A), R110.1
unnamed: D104.2 (A), R111.1
unnamed: D105.2 (A), R112.1
unnamed: D106.2 (A), R113.1
unnamed: D107.2 (A), R114.1
unnamed: D108.2 (A), R115.1
unnamed: D109.2 (A), R116.1
unnamed: D110.2 (A), R117.1
unnamed: D111.2 (A), R118.1
unnamed: D112.2 (A), R119.1
unnamed: D113.2 (A), R120.1
unnamed: D114.2 (A), R121.1
unnamed: D115.2 (A), R122.1
unnamed: D116.2 (A), R123.1
unnamed: D117.2 (A), R124.1
unnamed: D118.2 (A), R125.1
unnamed: D119.2 (A), R126.1
unnamed: D120.2 (A), R127.1
unnamed: D121.2 (A), R128.1
unnamed: D122.2 (A), R129.1
unnamed: D123.2 (A), R130.1
unnamed: D124.2 (A), R131.1
unnamed: D125.2 (A), R132.1
unnamed: D126.2 (A), R133.1
unnamed: D127.2 (A), R134.1
unnamed: D128.2 (A), R135.1
unnamed: D129.2 (A), R136.1
unnamed: D130.2 (A), R137.1
unnamed: IC1.15 (Q0), R1.2
unnamed: IC1.1 (Q1), R2.2
unnamed: IC1.2 (Q2), R3.2
unnamed: IC1.3 (Q3), R4.2
unnamed: IC1.4 (Q4), R5.2
unnamed: IC1.5 (Q5), R6.2
unnamed: IC1.6 (Q6), R7.2
unnamed: IC1.7 (Q7), R8.2
unnamed: IC2.15 (Q0), R41.2
unnamed: IC2.1 (Q1), R42.2
unnamed: IC2.2 (Q2), R43.2
unnamed: IC2.3 (Q3), R44.2
unnamed: IC2.4 (Q4), R45.2
unnamed: IC2.5 (Q5), R46.2
unnamed: IC2.6 (Q6), R47.2
unnamed: IC2.7 (Q7), R48.2
unnamed: IC3.15 (Q0), R9.2
unnamed: IC3.1 (Q1), R10.2
unnamed: IC3.2 (Q2), R11.2
unnamed: IC3.3 (Q3), R12.2
unnamed: IC3.4 (Q4), R13.2
unnamed: IC3.5 (Q5), R14.2
unnamed: IC3.6 (Q6), R15.2
unnamed: IC3.7 (Q7), R16.2
unnamed: IC4.15 (Q0), R49.2
unnamed: IC4.1 (Q1), R50.2
unnamed: IC4.2 (Q2), R51.2
unnamed: IC4.3 (Q3), R52.2
unnamed: IC4.4 (Q4), R53.2
unnamed: IC4.5 (Q5), R54.2
unnamed: IC4.6 (Q6), R55.2
unnamed: IC4.7 (Q7), R56.2
unnamed: IC5.15 (Q0), R17.2
unnamed: IC5.1 (Q1), R18.2
unnamed: IC5.2 (Q2), R19.2
unnamed: IC5.3 (Q3), R20.2
unnamed: IC5.4 (Q4), R21.2
unnamed: IC5.5 (Q5), R22.2
unnamed: IC5.6 (Q6), R23.2
unnamed: IC5.7 (Q7), R24.2
unnamed: IC6.15 (Q0), R57.2
unnamed: IC6.1 (Q1), R58.2
unnamed: IC6.2 (Q2), R59.2
unnamed: IC6.3 (Q3), R60.2
unnamed: IC6.4 (Q4), R61.2
unnamed: IC6.5 (Q5), R62.2
unnamed: IC6.6 (Q6), R63.2
unnamed: IC6.7 (Q7), R64.2
unnamed: IC7.15 (Q0), R25.2
unnamed: IC7.1 (Q1), R26.2
unnamed: IC7.2 (Q2), R27.2
unnamed: IC7.3 (Q3), R28.2
unnamed: IC7.4 (Q4), R29.2
unnamed: IC7.5 (Q5), R30.2
unnamed: IC7.6 (Q6), R31.2
unnamed: IC7.7 (Q7), R32.2
unnamed: IC8.15 (Q0), R33.2
unnamed: IC8.1 (Q1), R34.2
unnamed: IC8.2 (Q2), R35.2
unnamed: IC8.3 (Q3), R36.2
unnamed: IC8.4 (Q4), R37.2
unnamed: IC8.5 (Q5), R38.2
unnamed: IC8.6 (Q6), R39.2
unnamed: IC8.7 (Q7), R40.2
unnamed: IC9.2 (PROG), Rprog1.1
unnamed: IC9.7 (~CHRG), R74.2
unnamed: IC9.6 (~STDBY), R75.2
unnamed: IC10.15 (Q0), R65.2
unnamed: IC10.1 (Q1), R67.2
unnamed: IC10.2 (Q2), R71.2
unnamed: IC10.3 (Q3), R77.2
unnamed: IC10.4 (Q4), R78.2
unnamed: IC10.5 (Q5), R79.2
unnamed: IC10.6 (Q6), R80.2
unnamed: IC10.7 (Q7), R81.2
unnamed: IC11.15 (Q0), R82.2
unnamed: IC11.1 (Q1), R83.2
unnamed: IC11.2 (Q2), R84.2
unnamed: IC11.3 (Q3), R85.2
unnamed: IC11.4 (Q4), R86.2
unnamed: IC11.5 (Q5), R87.2
unnamed: IC11.6 (Q6), R88.2
unnamed: IC11.7 (Q7), R89.2
unnamed: IC12.15 (Q0), R90.2
unnamed: IC12.1 (Q1), R91.2
unnamed: IC12.2 (Q2), R92.2
unnamed: IC12.3 (Q3), R93.2
unnamed: IC12.4 (Q4), R94.2
unnamed: IC12.5 (Q5), R95.2
unnamed: IC12.6 (Q6), R96.2
unnamed: IC12.7 (Q7), R97.2
unnamed: IC13.15 (Q0), R98.2
unnamed: IC13.1 (Q1), R99.2
unnamed: IC13.2 (Q2), R100.2
unnamed: IC13.3 (Q3), R101.2
unnamed: IC13.4 (Q4), R102.2
unnamed: IC13.5 (Q5), R103.2
unnamed: IC13.6 (Q6), R104.2
unnamed: IC13.7 (Q7), R105.2
unnamed: IC14.15 (Q0), R106.2
unnamed: IC14.1 (Q1), R107.2
unnamed: IC14.2 (Q2), R108.2
unnamed: IC14.3 (Q3), R109.2
unnamed: IC14.4 (Q4), R110.2
unnamed: IC14.5 (Q5), R111.2
unnamed: IC14.6 (Q6), R112.2
unnamed: IC14.7 (Q7), R113.2
unnamed: IC15.15 (Q0), R114.2
unnamed: IC15.1 (Q1), R115.2
unnamed: IC15.2 (Q2), R116.2
unnamed: IC15.3 (Q3), R117.2
unnamed: IC15.4 (Q4), R118.2
unnamed: IC15.5 (Q5), R119.2
unnamed: IC15.6 (Q6), R120.2
unnamed: IC15.7 (Q7), R121.2
unnamed: IC16.15 (Q0), R122.2
unnamed: IC16.1 (Q1), R123.2
unnamed: IC16.2 (Q2), R124.2
unnamed: IC16.3 (Q3), R125.2
unnamed: IC16.4 (Q4), R126.2
unnamed: IC16.5 (Q5), R127.2
unnamed: IC16.6 (Q6), R128.2
unnamed: IC16.7 (Q7), R129.2
unnamed: IC17.15 (Q0), R130.2
unnamed: IC17.1 (Q1), R131.2
unnamed: IC17.2 (Q2), R132.2
unnamed: IC17.3 (Q3), R133.2
unnamed: IC17.4 (Q4), R134.2
unnamed: IC17.5 (Q5), R135.2
unnamed: IC17.6 (Q6), R136.2
unnamed: IC17.7 (Q7), R137.2
unnamed: LED1.1 (K), R74.1
unnamed: LED2.1 (K), R75.1
unnamed: U1.3 (OUTPUT), U2.4 (SENSOR_VP)
unnamed: R70.2, U2.34 (RXD0/IO3)
unnamed: U2.5 (SENSOR_VN), U3.3 (OUTPUT)
unnamed: R69.2, U2.35 (TXD0/IO1)
unnamed: C15.2, U4.10 (V3)
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

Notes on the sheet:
Note: Charging Current (mA) = 1100(V) / Rprog (kΩ)
SRX6
SRX1
SRX3
SoC
USB to UART
LED Pixels and Drivers LHS
Battery Charging
LED Pixels and Drivers RHS
SR4
SR7
SR1
SRX0
USB Input and Power Path Control
SR3
SR0
C473012
SR2
SRX5
SRX7
SR5
SRX4
SRX2
SR6

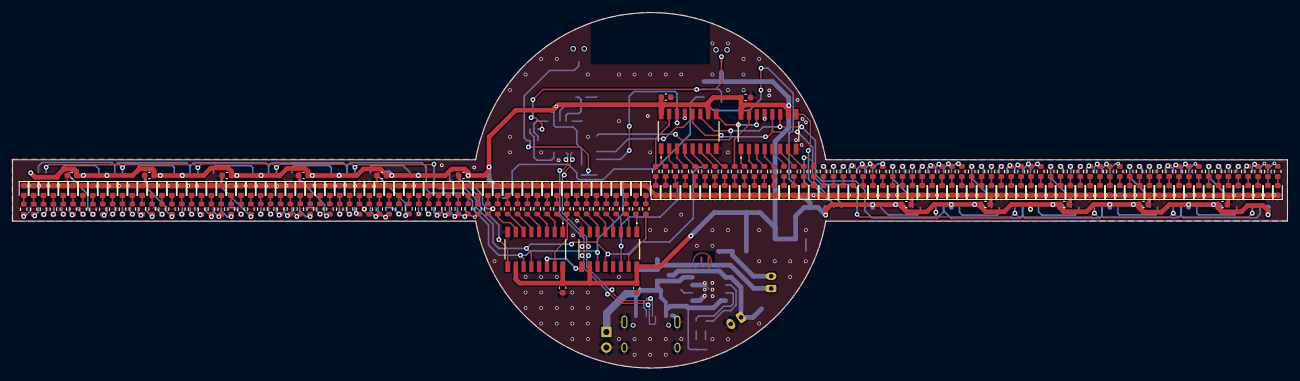
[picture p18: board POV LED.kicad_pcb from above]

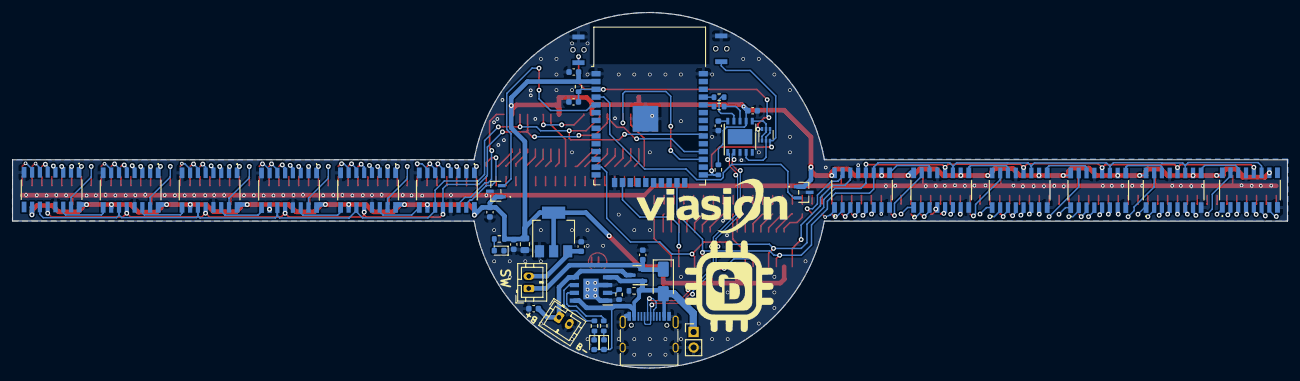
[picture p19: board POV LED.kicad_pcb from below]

Board: 2 copper layers, 208.0 x 58.0 mm, 324 parts (49 on the bottom side), 301 nets.

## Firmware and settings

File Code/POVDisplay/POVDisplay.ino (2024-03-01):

/*
 * Project Name: POV display 
 * Project Brief: Firmware for ESP32 POV Display. Display resolution 128 pixels
 * Author: Jobit Joseph
 * Copyright © Jobit Joseph
 * Copyright © Semicon Media Pvt Ltd
 * Copyright © Circuitdigest.com
 * 
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
 */
#include <Arduino.h>
#include <MultiShiftRegister.h>
#include "Images.h"
#include "Precompute.h"

// Pin Definitions
#define latchPin 14
#define clockPin 15
#define dataPin 13
#define latchPinx 17
#define clockPinx 18
#define dataPinx 16
#define HALL_SENSOR1_PIN 36
#define HALL_SENSOR2_PIN 39

// Global Variables
volatile unsigned long lastHallTrigger = 0;
volatile float rotationTime = 0;  // Time for one rotation in milliseconds
int hallSensor1State = 0;
int hallSensor2State = 0;
bool halfFrame = false;
int numberOfRegisters = 8;
int offset = 270;
int repeatvalue = 1;
int hys = 3000;
int frame = 0;
int repeat = 0;
int anim = 0;
int frameHoldTime = 1;     // Number of loops to hold each frame
int frameHoldCounter = 0;  // Counter to track loops for current frame

//Shift register Driver instances for both hands
MultiShiftRegister msr(numberOfRegisters, latchPin, clockPin, dataPin);
MultiShiftRegister msrx(numberOfRegisters, latchPinx, clockPinx, dataPinx);

//Function to calculate polar co-ordintes, and get corresponding data from the arrays.
int getValueFromAngle(const uint8_t arrayName[][16], int angle, int radius) {
  // Adjust the angle by subtracting offset to rotate counter-clockwise
  int adjustedAngle = angle - offset;
  if (adjustedAngle < 0) adjustedAngle += 360;  // Ensure the angle stays within 0-359 degrees

  // Invert the targetX calculation to flip the image horizontally
  int targetX = 127 - precomputedCos[radius][adjustedAngle];  // Flipping targetX
  int targetY = precomputedSin[radius][adjustedAngle];
  if (targetX >= 0 && targetX < 128 && targetY >= 0 && targetY < 128) {
    int byteIndex = targetX / 8;
    int bitIndex = 7 - (targetX % 8);
    return (arrayName[targetY][byteIndex] >> bitIndex) & 1;  // Extract the bit value and return it
  } else {
    return -1;  // Out of bounds
  }
}

//Hall sensor 1 interrupt routine
void ISR_HallSensor1() {
  unsigned long currentTime = micros();
  // Check if HYS ms have passed since the last trigger
  if (currentTime - lastHallTrigger >= hys) {
    rotationTime = (currentTime - lastHallTrigger) / 1000.0;
    lastHallTrigger = currentTime;
    hallSensor1State = 1;
    halfFrame = true;
  }
}

//Hall sensor 2 interrupt routine
void ISR_HallSensor2() {
  unsigned long currentTime = micros();
  // Check if HYS ms have passed since the last trigger
  if (currentTime - lastHallTrigger >= hys) {
    lastHallTrigger = currentTime;
    hallSensor2State = 1;
    halfFrame = false;
  }
}

//Function to calculate RPM and display each frame accordingly 
void DisplayFrame(const uint8_t ImageName[][16]) {
  float timePerSegment = rotationTime / 360.0;  // Assuming 180 segments per half rotation

  for (int i = 0; i < 180; i++) {
    unsigned long segmentStartTime = micros();

    for (int j = 0; j < 64; j++) {
      // First arm (msr) displays the first half of the frame
      if (getValueFromAngle(ImageName, i + (halfFrame ? 0 : 180), j)) {
        msr.set(j);
      } else {
        msr.clear(j);
      }

      // Second arm (msrx) displays the second half of the frame
      if (getValueFromAngle(ImageName, i + (halfFrame ? 180 : 0), j)) {
        msrx.set(j);
      } else {
        msrx.clear(j);
      }
    }

    msr.shift();
    msrx.shift();

    while (micros() - segmentStartTime < timePerSegment * 1000)
      ;
  }
}

void setup() {
  // Initialize pins
  pinMode(latchPin, OUTPUT);
  pinMode(clockPin, OUTPUT);
  pinMode(dataPin, OUTPUT);
  pinMode(latchPinx, OUTPUT);
  pinMode(clockPinx, OUTPUT);
  pinMode(dataPinx, OUTPUT);
  pinMode(HALL_SENSOR1_PIN, INPUT);
  pinMode(HALL_SENSOR2_PIN, INPUT);

  attachInterrupt(digitalPinToInterrupt(HALL_SENSOR1_PIN), ISR_HallSensor1, RISING);
  attachInterrupt(digitalPinToInterrupt(HALL_SENSOR2_PIN), ISR_HallSensor2, RISING);
  for (int i = 0; i < 64; i++) {
    msr.clear(i);
    msrx.clear(i);
  }
  msr.shift();
  msrx.shift();
  Serial.begin(115200);
}

void loop() {
  if (hallSensor1State || hallSensor2State) {
    if (anim == 0) {
      DisplayFrame(CDArrays[frame]);
      // Increment the counter
      frameHoldCounter++;
      // Check if it's time to move to the next frame
      if (frameHoldCounter >= frameHoldTime) {
        // Reset the counter
        frameHoldCounter = 0;
        // Move to the next frame
        frame++;
        if (frame > 21) {
          frame = 0;
          repeat++;
          if (repeat == 1) {
            repeat = 0;
            anim++;
            frameHoldTime = 1;
            repeatvalue = 1;
          }
        }
      }
    }
    if (anim == 1) {
      DisplayFrame(ImageCD_22);
      // Increment the counter
      frameHoldCounter++;
      // Check if it's time to move to the next frame
      if (frameHoldCounter >= frameHoldTime) {
        // Reset the counter
        frameHoldCounter = 0;
        // Move to the next frame
        frame++;
        if (frame > 50) {
          frame = 0;
          repeat++;
          if (repeat == repeatvalue) {
            repeat = 0;
            anim++;
            frameHoldTime = 2;
            repeatvalue = 1;
          }
        }
      }
    }
    if (anim == 2) {
      DisplayFrame(ViasionArrays[frame]);
      // Increment the counter
      frameHoldCounter++;
      // Check if it's time to move to the next frame
      if (frameHoldCounter >= frameHoldTime) {
        // Reset the counter
        frameHoldCounter = 0;
        // Move to the next frame
        frame++;
        if (frame > 21) {
          frame = 0;
          repeat++;
          if (repeat == repeatvalue) {
            repeat = 0;
            anim++;
            frameHoldTime = 1;
            repeatvalue = 1;
          }
        }
      }
    }
    if (anim == 3) {
      DisplayFrame(Image_Viasion22);
      // Increment the counter
      frameHoldCounter++;
      // Check if it's time to move to the next frame
      if (frameHoldCounter >= frameHoldTime) {
        // Reset the counter
        frameHoldCounter = 0;
        // Move to the next frame
        frame++;
        if (frame > 50) {
          frame = 0;
          repeat++;
          if (repeat == repeatvalue) {
            repeat = 0;
            anim++;
            frameHoldTime = 2;
            repeatvalue = 1;
          }
        }
      }
    }
    if (anim == 4) {
      DisplayFrame(ViasionOTRArrays[frame]);
      // Increment the counter
      frameHoldCounter++;
      // Check if it's time to move to the next frame
      if (frameHoldCounter >= frameHoldTime) {
        // Reset the counter
        frameHoldCounter = 0;
        // Move to the next frame
        frame++;
        if (frame > 11) {
          frame = 0;
          repeat++;
          if (repeat == repeatvalue) {
            repeat = 0;
            anim++;
            frameHoldTime = 1;
            repeatvalue = 10;
          }
        }
      }
    }
    if (anim == 5) {
      DisplayFrame(CatRunArray[frame]);
      // Increment the counter
      frameHoldCounter++;
      // Check if it's time to move to the next frame
      if (frameHoldCounter >= frameHoldTime) {
        // Reset the counter
        frameHoldCounter = 0;
        // Move to the next frame
        frame++;
        if (frame > 9) {
          frame = 0;
          repeat++;
          if (repeat == repeatvalue) {
            repeat = 0;
            anim++;
            frameHoldTime = 2;
            repeatvalue = 2;
          }
        }
      }
    } else if (anim == 6) {
      DisplayFrame(CatArrays[frame]);
      // Increment the counter
      frameHoldCounter++;
      // Check if it's time to move to the next frame
      if (frameHoldCounter >= frameHoldTime) {
        // Reset the counter
        frameHoldCounter = 0;
        // Move to the next frame
        frame++;
        if (frame > 61) {
          frame = 0;
          repeat++;
          if (repeat == repeatvalue) {
            repeat = 0;
            anim++;
            frameHoldTime = 2;
            repeatvalue = 3;
          }
        }
      }
    } else if (anim == 7) {
      DisplayFrame(RunningSFArrays[frame]);
      // Increment the counter
      frameHoldCounter++;
      // Check if it's time to move to the next frame
      if (frameHoldCounter >= frameHoldTime) {
        // Reset the counter
        frameHoldCounter = 0;
        // Move to the next frame
        frame++;
        if (frame > 11) {
          frame = 0;
          repeat++;
          if (repeat == repeatvalue) {
            repeat = 0;
            anim++;
            frameHoldTime = 2;
            repeatvalue = 1;
          }
        }
      }
    } else if (anim == 8) {
      DisplayFrame(Dance1Arrays[frame]);
      // Increment the counter
      frameHoldCounter++;
      // Check if it's time to move to the next frame
      if (frameHoldCounter >= frameHoldTime) {
        // Reset the counter
        frameHoldCounter = 0;
        // Move to the next frame
        frame++;
        if (frame > 93) {
          frame = 0;
          repeat++;
          if (repeat == repeatvalue) {
            repeat = 0;
            anim++;
            frameHoldTime = 1;
            repeatvalue = 4;
          }
        }
      }
    } else if (anim == 9) {
      DisplayFrame(EYEArrays[frame]);  // Increment the counter
      frameHoldCounter++;
      // Check if it's time to move to the next frame
      if (frameHoldCounter >= frameHoldTime) {
        // Reset the counter
        frameHoldCounter = 0;
        // Move to the next frame
        frame++;
        if (frame > 73) {
          frame = 0;
          repeat++;
          if (repeat == repeatvalue) {
            repeat = 0;
            anim++;
            frameHoldTime = 2;
            repeatvalue = 4;
          }
        }
      }
    } else if (anim == 10) {
      DisplayFrame(GlobexArrays[frame]);  // Increment the counter
      frameHoldCounter++;
      // Check if it's time to move to the next frame
      if (frameHoldCounter >= frameHoldTime) {
        // Reset the counter
        frameHoldCounter = 0;
        // Move to the next frame
        frame++;
        if (frame > 14) {
          frame = 0;
          repeat++;
          if (repeat == repeatvalue) {
            repeat = 0;
            anim++;
            frameHoldTime = 20;
            repeatvalue = 1;
          }
        }
      }
    } else if (anim == 11) {
      DisplayFrame(ClockArrays[frame]);  // Increment the counter
      frameHoldCounter++;
      // Check if it's time to move to the next frame
      if (frameHoldCounter >= frameHoldTime) {
        // Reset the counter
        frameHoldCounter = 0;
        // Move to the next frame
        frame++;
        if (frame > 13) {
          frame = 0;
          repeat++;
          if (repeat == repeatvalue) {
            repeat = 0;
            anim = 0;
            frameHoldTime = 2;
            repeatvalue = 1;
          }
        }
      }
    }
    hallSensor1State = 0;
    hallSensor2State = 0;
  }
}

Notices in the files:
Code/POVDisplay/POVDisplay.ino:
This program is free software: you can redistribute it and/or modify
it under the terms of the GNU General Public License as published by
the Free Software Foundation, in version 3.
